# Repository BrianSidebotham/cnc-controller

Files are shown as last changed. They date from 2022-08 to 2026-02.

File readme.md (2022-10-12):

# CNC Controller

This CNC controller is an expansion board for LinuxCNC. See the [electronics](electronics/readme.md) section for the RPi GPIO expansion board suitable for use with LinuxCNC using the [configuration](linuxcnc-configuration/denford-orac-rpi/readme.md).

The PCB is an opto-isolation IO expansion board featuring:

- 16 Opto-isolated outputs (With indicator LED)
- 8 opto-isolated inputs (With indicator LED)
- 2 0-10V analogue outputs connected to two of the opto-isolated outputs

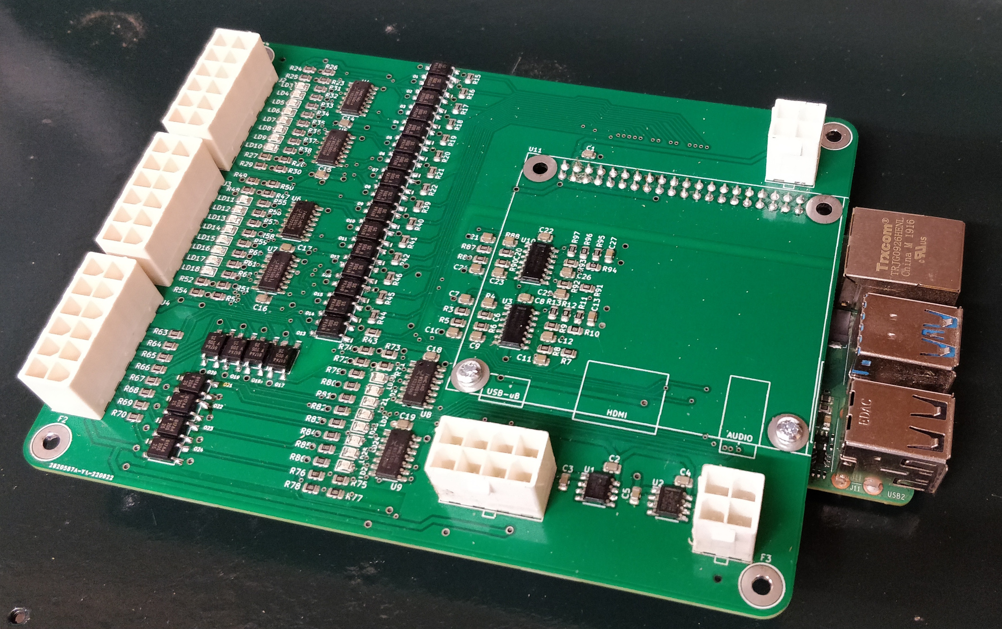
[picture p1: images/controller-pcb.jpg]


## KiCAD Parts Library

This project relies on my KiCAD parts library. So you will need to also clone a copy of my
[KiCAD parts library](https://github.com/BrianSidebotham/kicad-parts).

Then, you can tell KiCAD where to find the parts library by creating a new environment
variable called `KICAD_BJS_KICAD_PARTS` and set the value to the path to the parts library.

If you get the value or variable name wrong you'll see a lot of missing symbols in the
project.

## Build LinuxCNC

You can go ahead and download the LinuxCNC Distribution or else you can build yourself an up-to-date version.

In order to get an up-to-date version, download the LinuxCNC RPi image and write it to an SD Card.

Boot the card and then do the following to update the LinuxCNC package:

```shell
$ wget https://www.linuxcnc.org/dists/buster/2.8-rtpreempt/binary-armhf/linuxcnc-uspace_2.8.4_armhf.deb
$ sudo dpkg -i ./linuxcnc-uspace_2.8.4_armhf.deb
```

## Future Buildroot

In order to build an OS specifically for LinuxCNC you can use the following instructions:

>**WARNING**: These instructions are for future use, do not use yet.

```shell
$ wget https://buildroot.org/downloads/buildroot-2022.02.5.tar.gz
$ tar xf buildroot-2022.02.5.tar.gz
$ cd buildroot-2022.02.5
$ make raspberrypi4_64_defconfig
```

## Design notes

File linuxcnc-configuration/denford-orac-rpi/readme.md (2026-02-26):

# Denford ORAC Linux CNC Configuration

This directory contains HAL files for the hardware in this project and specifically for Denford ORAC hardware.

## Getting Started

Download the Linux CNC 2.9.8 RPI4 or RPI5 image with PREEMPT_RT from the linuxcnc downloads section

> [!NOTE]
> The difference between an RPi4 and RPi5 here is significant. I highly recommend you use an
> RPi5 for a linuxcnc machine using this configuration and image, but I have run LinuxCNC 2.9.3
> like this on an RPi4 for a couple of years so it certainly does work.

Write the image to an SD card by extracting it and then writing to the SD card

> [!WARN]
> _PLEASE_ use `lsblk` to determine what block device the SD Card is. For my machine which only has an NVME drive as the root, this enumerates as `/dev/sda` which is extremely risky if as you're about to overwrite a complete disk. Make sure it's the correct one before running the command:

```sh
unzip image_2026-01-21-raspios-lcnc-2.9.8-trixie-arm64.zip 
sudo su -
cat ./2026-01-21-raspios-lcnc-2.9.8-trixie-arm64.img > /dev/sda \
    && sync \
    && eject /dev/sda
```

With the card written, insert it into the Linux CNC RPi and go through the initial setup. I also recommend setting up the ssh service so you can remotely administer the lathe:

```sh
sudo systemctl enable ssh
sudo systemctl start ssh
```

Log in through SSH and disable the hardware intefaces that are defaulted to on so you do not have conflicting GPIO pins. Make sure the following settings are correct in `/boot/firmware/config.txt`:

```
dtparam=i2c_arm=off
dtparam=spi=off
```

Once logged in, you can clone this repository in the home directory and then start up linux CNC. If you've wired everything the same as the schematics and wiring diagram shows, then you can start the linuxcnc session using:

```sh
cd /home/cnc/cnc-controller/linuxcnc-configuration/denford-orac-rpi/
./linuxcnc.sh
```

## LatheMacros Python Dependencies (Debian Trixie)

If the Cycles tab fails with `ValueError: Namespace Rsvg not available`, install the required **system** packages (no venv required):

```sh
sudo apt update
sudo apt install -y python3-gi gir1.2-rsvg-2.0 python3-cairo
```

Optional (removes the non-fatal GTK warning `Failed to load module "canberra-gtk-module"`):

```sh
sudo apt install -y libcanberra-gtk-module libcanberra-gtk3-module
```

Quick verification:

```sh
python3 -c "import gi, cairo; gi.require_version('Rsvg','2.0'); from gi.repository import Rsvg; print('OK: Rsvg + cairo available')"
```

So if you so happen to have a Denford Orac then this'll _just work_.

## Stepper Motor Scales

The stepper motors on the Denford ORAC are standard 1.8deg / step NEMA34 which have `(360 / 1.8)` 200 steps per revolution.

The [MSD752](../manuals/MSD752_stepper_drive.pdf) drivers I'm using have been configured for 4x microstepping to give 800 steps per rev.

The stepper motors do not directly drive the axis, instead they drive the axis through a belt and pulley setup. The [ORAC operating and maintenance manual](../manuals/orac-programming-operating-and-maintenance.pdf) details the size of the pulleys.

### X Axis

For the X cross slide we have the following arrangement

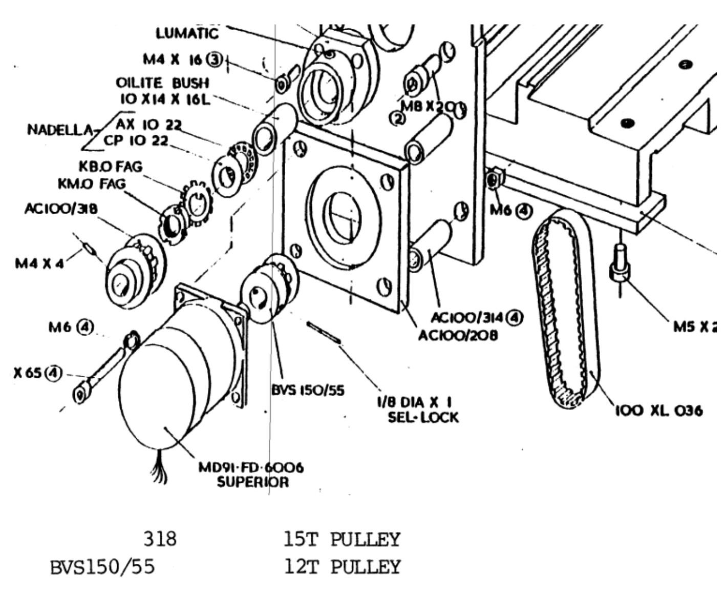
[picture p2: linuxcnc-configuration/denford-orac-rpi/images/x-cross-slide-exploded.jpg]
X Cross-Slide


With the stepper using 800 turns per we can calculate the scale for the x-axis stepper motor stepgen.

The ballscrew is 8mm x 2.5mm pitch

Calculate the number of steps it takes to make a complete revolution of the ballscrew through the pulleys with the motor and driver using 800 steps per rev:

    800 * (15/12) = 1000

One revolution of the ballscrew will move the carriage 2.5mm and we want to know how many steps are required to complete one unit of measurement in the HAL. For me, that's 1mm as everything is metric for me.

    1000 / 2.5 = 400

This gives each step a distance of `0.0025mm`

### Z Axis

For the Z axis we have the following arrangement

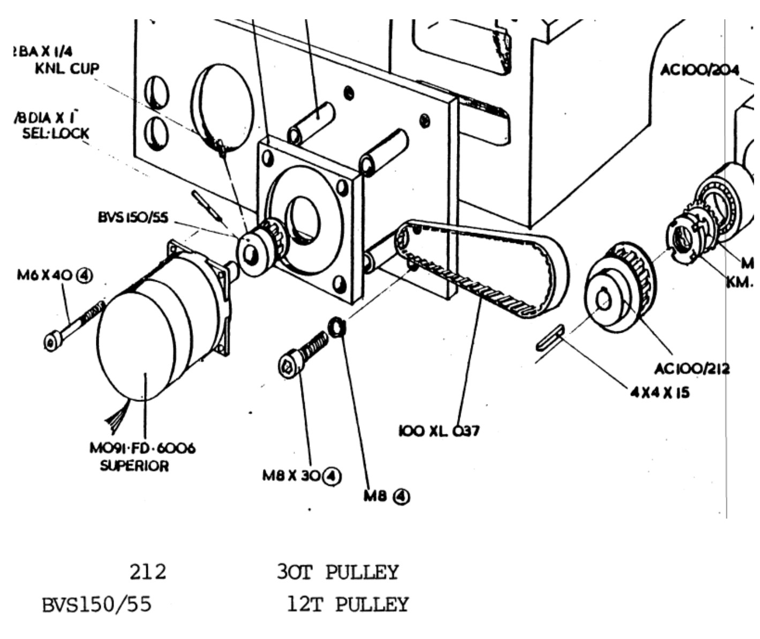
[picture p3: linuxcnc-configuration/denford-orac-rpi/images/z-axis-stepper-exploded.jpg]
Z Axis


The ballscree is 20mm x 5mm pitch

Calculate the number of steps it takes to make a complete revolution of the ballscrew through the pulleys with the motor and driver using 800 steps per rev:

    800 * (30 / 12) = 2000

One revolution of the ballscrew will move the carriage 5mm and we want to know how many steps are required to complete one unit of measurement in the HAL. For me, that's 1mm as everything is metric for me.

    2000 / 5 = 400

This gives each step a distance of `0.0025mm`

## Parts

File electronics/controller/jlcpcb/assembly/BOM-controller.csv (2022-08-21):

Comment | Designator | Footprint | LCSC
1u | C10,C11,C12,C13,C20,C21,C23,C24,C25,C26,C27,C6,C7,C9 | C_0805_2012Metric | C28323
100n | C1,C14,C15,C16,C17,C18,C19,C2,C22,C3,C4,C5,C8 | C_0805_2012Metric | C49678
74HC14 | U4,U5,U6,U7,U8,U9 | SOIC-14_3.9x8.7mm_P1.27mm | C5605
TEVALULOK4W | J1 | te-connectivity_val-u-lok_vertical_4_1586768-4
TEVALULOK4W | J8 | te-connectivity_val-u-lok_vertical_4_1586768-4
TEVALULOK8W | J10 | te-connectivity_val-u-lok_vertical_8_1586768-8
RESISTOR | R1 | R_0805_2012Metric
2k2 | R2 | R_0805_2012Metric
68k | R3 | R_0805_2012Metric
68k | R4 | R_0805_2012Metric
68k | R5 | R_0805_2012Metric
68k | R6 | R_0805_2012Metric
68k | R7 | R_0805_2012Metric
68k | R8 | R_0805_2012Metric
68k | R9 | R_0805_2012Metric
1k5 | R10 | R_0805_2012Metric
120k | R11 | R_0805_2012Metric
120k | R13 | R_0805_2012Metric
1k | R23 | R_0805_2012Metric
MC33204 | U3 | SOIC-14_3.9x8.7mm_P1.27mm
1k5 | R12 | R_0805_2012Metric
VOM617A-4T | O10 | VOMOPTO
VOM617A-4T | O9 | VOMOPTO
78L10SMD | U2 | SOIC-8_3.9x4.9mm_P1.27mm
LED | LD1 | LED_0805_2012Metric
LED | LD2 | LED_0805_2012Metric
LED | LD3 | LED_0805_2012Metric
LED | LD4 | LED_0805_2012Metric
LED | LD10 | LED_0805_2012Metric
LED | LD19 | LED_0805_2012Metric
LED | LD20 | LED_0805_2012Metric
LED | LD21 | LED_0805_2012Metric
LED | LD23 | LED_0805_2012Metric
LED | LD24 | LED_0805_2012Metric
LED | LD25 | LED_0805_2012Metric
LED | LD26 | LED_0805_2012Metric
VOM617A-4T | O13 | VOMOPTO
VOM617A-4T | O14 | VOMOPTO
VOM617A-4T | O16 | VOMOPTO
VOM617A-4T | O17 | VOMOPTO
VOM617A-4T | O19 | VOMOPTO
VOM617A-4T | O20 | VOMOPTO
VOM617A-4T | O21 | VOMOPTO
VOM617A-4T | O23 | VOMOPTO
1k | R26 | R_0805_2012Metric
1k | R28 | R_0805_2012Metric
1k | R30 | R_0805_2012Metric
330R | R34 | R_0805_2012Metric
330R | R35 | R_0805_2012Metric
330R | R36 | R_0805_2012Metric
330R | R37 | R_0805_2012Metric
330R | R38 | R_0805_2012Metric
680R | R39 | R_0805_2012Metric
680R | R40 | R_0805_2012Metric
680R | R41 | R_0805_2012Metric
680R | R42 | R_0805_2012Metric
680R | R43 | R_0805_2012Metric
680R | R44 | R_0805_2012Metric
680R | R45 | R_0805_2012Metric
680R | R46 | R_0805_2012Metric
1k | R47 | R_0805_2012Metric
1k | R48 | R_0805_2012Metric
1k | R49 | R_0805_2012Metric
1k | R50 | R_0805_2012Metric
1k | R51 | R_0805_2012Metric
1k | R52 | R_0805_2012Metric
1k | R53 | R_0805_2012Metric
680R | R63 | R_0805_2012Metric
680R | R64 | R_0805_2012Metric
680R | R65 | R_0805_2012Metric
680R | R68 | R_0805_2012Metric
680R | R69 | R_0805_2012Metric
680R | R70 | R_0805_2012Metric
1k | R71 | R_0805_2012Metric
1k | R73 | R_0805_2012Metric
1k | R74 | R_0805_2012Metric
1k | R75 | R_0805_2012Metric
1k | R76 | R_0805_2012Metric
1k | R77 | R_0805_2012Metric
1k | R78 | R_0805_2012Metric
330R | R79 | R_0805_2012Metric
330R | R80 | R_0805_2012Metric
330R | R81 | R_0805_2012Metric
330R | R82 | R_0805_2012Metric
330R | R83 | R_0805_2012Metric
330R | R84 | R_0805_2012Metric
68k | R88 | R_0805_2012Metric
68k | R89 | R_0805_2012Metric
68k | R90 | R_0805_2012Metric
68k | R91 | R_0805_2012Metric
68k | R92 | R_0805_2012Metric
68k | R93 | R_0805_2012Metric
1k5 | R94 | R_0805_2012Metric
120k | R95 | R_0805_2012Metric
1k5 | R96 | R_0805_2012Metric
120k | R97 | R_0805_2012Metric
330R | R98 | R_0805_2012Metric
MC33204 | U10 | SOIC-14_3.9x8.7mm_P1.27mm
VOM617A-4T | O11 | VOMOPTO
RPI40PIN | U11 | rpi-40pin
330R | R32 | R_0805_2012Metric
330R | R33 | R_0805_2012Metric
330R | R31 | R_0805_2012Metric
VOM617A-4T | O5 | VOMOPTO
VOM617A-4T | O6 | VOMOPTO
VOM617A-4T | O7 | VOMOPTO
VOM617A-4T | O8 | VOMOPTO
680R | R19 | R_0805_2012Metric
680R | R20 | R_0805_2012Metric
680R | R21 | R_0805_2012Metric
680R | R22 | R_0805_2012Metric
1k | R24 | R_0805_2012Metric
1k | R25 | R_0805_2012Metric
1k | R27 | R_0805_2012Metric
1k | R29 | R_0805_2012Metric
LED | LD8 | LED_0805_2012Metric
LED | LD7 | LED_0805_2012Metric
LED | LD6 | LED_0805_2012Metric
TEVALULOK12W | J2 | te-connectivity_val-u-lok_vertical_12_1-1586768-2
LED | LD9 | LED_0805_2012Metric
LED | LD5 | LED_0805_2012Metric
VOM617A-4T | O12 | VOMOPTO
VOM617A-4T | O15 | VOMOPTO
VOM617A-4T | O18 | VOMOPTO
VOM617A-4T | O22 | VOMOPTO
VOM617A-4T | O24 | VOMOPTO
VOM617A-4T | O1 | VOMOPTO
VOM617A-4T | O2 | VOMOPTO
VOM617A-4T | O3 | VOMOPTO
VOM617A-4T | O4 | VOMOPTO
680R | R15 | R_0805_2012Metric
680R | R16 | R_0805_2012Metric
680R | R17 | R_0805_2012Metric
680R | R18 | R_0805_2012Metric
TEVALULOK12W | J3 | te-connectivity_val-u-lok_vertical_12_1-1586768-2
LED | LD12 | LED_0805_2012Metric
LED | LD13 | LED_0805_2012Metric
LED | LD14 | LED_0805_2012Metric
LED | LD15 | LED_0805_2012Metric
LED | LD16 | LED_0805_2012Metric
LED | LD17 | LED_0805_2012Metric
LED | LD18 | LED_0805_2012Metric
330R | R55 | R_0805_2012Metric
330R | R57 | R_0805_2012Metric
330R | R58 | R_0805_2012Metric
330R | R59 | R_0805_2012Metric
330R | R60 | R_0805_2012Metric
330R | R61 | R_0805_2012Metric
330R | R62 | R_0805_2012Metric
LED | LD11 | LED_0805_2012Metric
TEVALULOK12W | J4 | te-connectivity_val-u-lok_vertical_12_1-1586768-2
330R | R56 | R_0805_2012Metric
1k | R54 | R_0805_2012Metric
680R | R66 | R_0805_2012Metric
680R | R67 | R_0805_2012Metric
LED | LD22 | LED_0805_2012Metric
330R | R85 | R_0805_2012Metric
330R | R86 | R_0805_2012Metric
68k | R87 | R_0805_2012Metric
1k | R72 | R_0805_2012Metric
78L05SMD | U1 | SOIC-8_3.9x4.9mm_P1.27mm
330R | R14 | R_0805_2012Metric
M3 | F3 | M3
M3 | F4 | M3
M3 | F2 | M3
M3 | F1 | M3

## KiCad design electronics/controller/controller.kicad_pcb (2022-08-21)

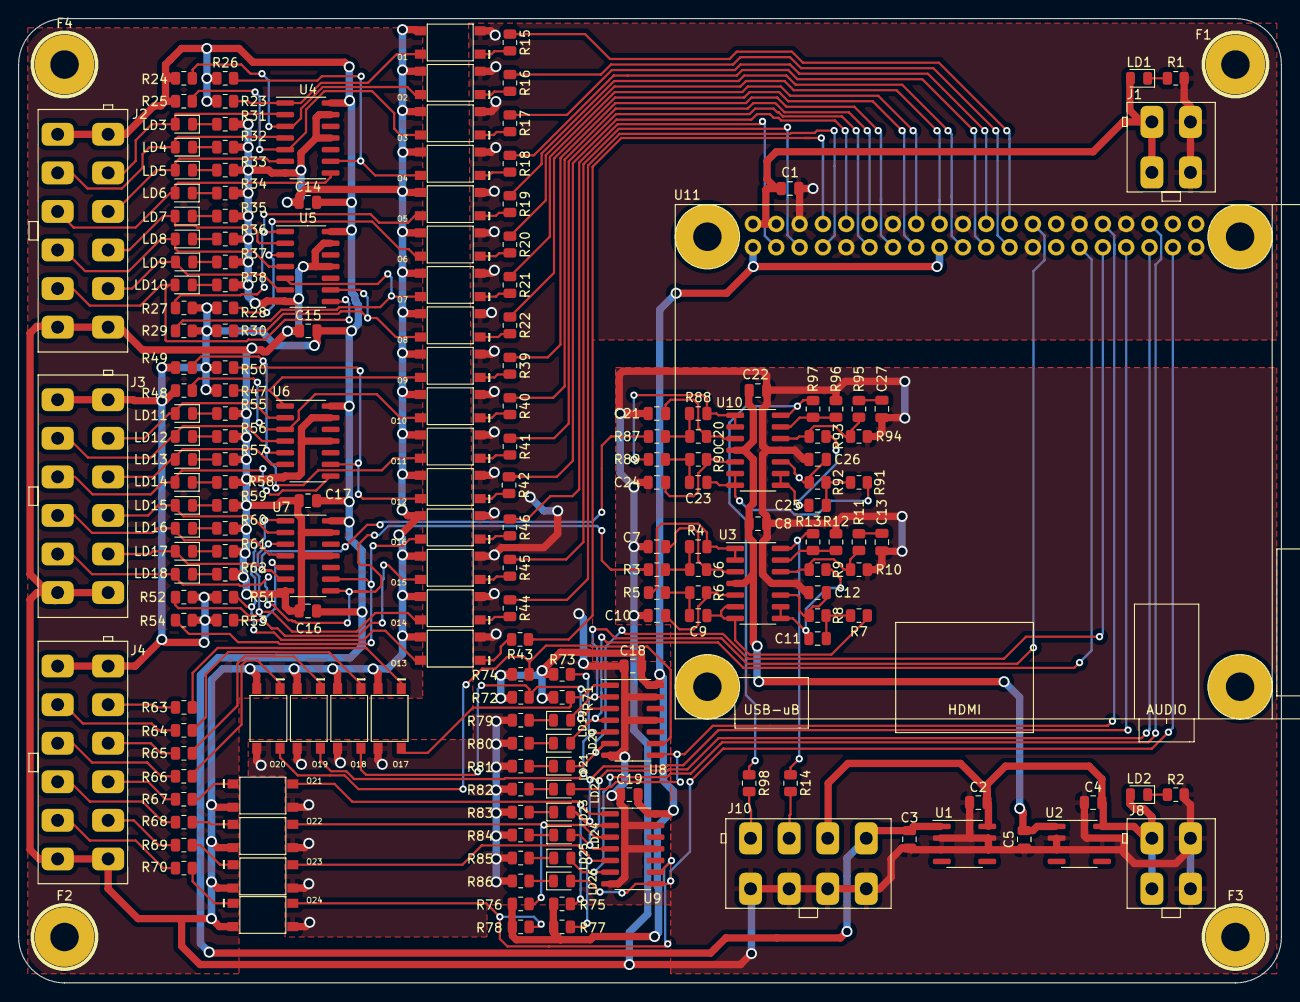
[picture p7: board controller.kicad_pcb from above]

Board: 2 copper layers, 137.5 x 105.0 mm, 196 parts (0 on the bottom side), 157 nets.

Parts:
C1, C2, C3, C4, C5, C8, C14, C15, C16, C17, C18, C19, C22: 100n; C_0805_2012Metric
C6, C7, C9, C10, C11, C12, C13, C20, C21, C23, C24, C25, C26, C27: 1u; C_0805_2012Metric
F1, F2, F3, F4: M3
J1, J8: TEVALULOK4W; te-connectivity_val-u-lok_vertical_4_1586768-4
J2, J3, J4: TEVALULOK12W; te-connectivity_val-u-lok_vertical_12_1-1586768-2
J10: TEVALULOK8W; te-connectivity_val-u-lok_vertical_8_1586768-8
LD1, LD2, LD3, LD4, LD5, LD6, LD7, LD8, LD9, LD10, LD11, LD12, LD13, LD14, LD15, LD16, LD17, LD18, LD19, LD20, LD21, LD22, LD23, LD24, LD25, LD26: LED; LED_0805_2012Metric
O1, O2, O3, O4, O5, O6, O7, O8, O9, O10, O11, O12, O13, O14, O15, O16, O17, O18, O19, O20, O21, O22, O23, O24: VOM617A-4T; VOMOPTO
R1: RESISTOR; R_0805_2012Metric
R2: 2k2; R_0805_2012Metric
R3, R4, R5, R6, R7, R8, R9, R87, R88, R89, R90, R91, R92, R93: 68k; R_0805_2012Metric
R10, R12, R94, R96: 1k5; R_0805_2012Metric
R11, R13, R95, R97: 120k; R_0805_2012Metric
R14, R31, R32, R33, R34, R35, R36, R37, R38, R55, R56, R57, R58, R59, R60, R61, R62, R79, R80, R81, R82, R83, R84, R85, R86, R98: 330R; R_0805_2012Metric
R15, R16, R17, R18, R19, R20, R21, R22, R39, R40, R41, R42, R43, R44, R45, R46, R63, R64, R65, R66, R67, R68, R69, R70: 680R; R_0805_2012Metric
R23, R24, R25, R26, R27, R28, R29, R30, R47, R48, R49, R50, R51, R52, R53, R54, R71, R72, R73, R74, R75, R76, R77, R78: 1k; R_0805_2012Metric
U1: 78L05SMD; SOIC-8_3.9x4.9mm_P1.27mm
U2: 78L10SMD; SOIC-8_3.9x4.9mm_P1.27mm
U3, U10: MC33204; SOIC-14_3.9x8.7mm_P1.27mm
U4, U5, U6, U7, U8, U9: 74HC14; SOIC-14_3.9x8.7mm_P1.27mm
U11: RPI40PIN; rpi-40pin

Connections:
+10V: C5.2, C8.2, C22.2, U2.1 (VO), U3.4 (VCC), U10.4 (VCC)
+12V: C2.2, C4.2, J8.1, J8.2, J10.5, LD2.2, U1.8 (VIN), U2.8 (VIN)
/0-10V-CH1: J10.1, R98.2
/0-10V-CH2: J10.3, R14.2
/IN1: J4.3, R63.1
/IN2: J4.4, R64.1
/IN3: J4.5, R65.1
/IN4: J4.6, R66.1
/IN5: J4.7, R67.1
/IN6: J4.8, R68.1
/IN7: J4.9, R69.1
/IN8: J4.10, R70.1
/OUT1: J2.3, LD3.2, U4.2
/OUT2: J2.4, LD4.2, U4.4
/OUT3: J2.5, LD5.2, U4.6
/OUT4: J2.6, LD6.2, U4.8
/OUT5: J2.7, LD7.2, U5.2
/OUT6: J2.8, LD8.2, U5.4
/OUT7: J2.9, LD9.2, U5.6
/OUT8: J2.10, LD10.2, U5.8
/OUT9: J3.3, LD11.2, U6.2
/OUT10: J3.4, LD12.2, U6.4
/OUT11: J3.5, LD13.2, U6.6
/OUT12: J3.6, LD14.2, U6.8
/OUT13: J3.7, LD15.2, U7.2
/OUT14: J3.8, LD16.2, U7.4
/OUT15: J3.9, LD17.2, R87.1, U7.6
/OUT16: J3.10, LD18.2, R3.1, U7.8
/RPIIN1: LD19.2, U8.2, U11.26 (GPIO7)
/RPIIN2: LD20.2, U8.4, U11.29 (GPIO5)
/RPIIN3: LD21.2, U8.6, U11.31 (GPIO6)
/RPIIN4: LD22.2, U8.8, U11.32 (GPIO12)
/RPIIN5: LD23.2, U9.2, U11.33 (GPIO13)
/RPIIN6: LD24.2, U9.4, U11.35 (GPIO19)
/RPIIN7: LD25.2, U9.6, U11.36 (GPIO16)
/RPIIN8: LD26.2, U9.8, U11.37 (GPIO26)
/RPIOUT1: R15.1, U11.24 (GPIO8)
/RPIOUT2: R16.1, U11.23 (GPIO11)
/RPIOUT3: R17.1, U11.22 (GPIO25)
/RPIOUT4: R18.1, U11.21 (GPIO9)
/RPIOUT5: R19.1, U11.19 (GPIO10)
/RPIOUT6: R20.1, U11.18 (GPIO24)
/RPIOUT7: R21.1, U11.16 (GPIO23)
/RPIOUT8: R22.1, U11.15 (GPIO22)
/RPIOUT9: R39.1, U11.13 (GPIO27)
/RPIOUT10: R40.1, U11.12 (GPIO18)
/RPIOUT11: R41.1, U11.11 (GPIO17)
/RPIOUT12: R42.1, U11.10 (GPIO15)
/RPIOUT13: R43.1, U11.8 (GPIO14)
/RPIOUT14: R44.1, U11.7 (GPIO4)
/RPIOUT15: R45.1, U11.5 (GPIO3)
/RPIOUT16: R46.1, U11.3 (GPIO2)
/rpiconnectivity/3V3: C18.2, C19.2, R71.2, R72.2, R73.2, R74.2, R75.2, R76.2, R77.2, R78.2, U8.14 (VCC), U9.14 (VCC), U11.1 (3V3), U11.17 (3V3)
GND: C1.1, C18.1, C19.1, J1.3, J1.4, O1.2, O2.2, O3.2, O4.2, O5.2, O6.2, O7.2, O8.2, O9.2, O10.2, O11.2, O12.2, O13.2, O14.2, O15.2, O16.2, O17.3, O18.3, O19.3, O20.3, O21.3, O22.3, O23.3, O24.3, R1.2, R79.2, R80.2, R81.2, R82.2, R83.2, R84.2, R85.2, R86.2, U8.7 (GND), U8.11, U8.13, U9.7 (GND), U9.11, U9.13, U11.6 (GND), U11.9 (GND), U11.14 (GND), U11.20 (GND), U11.25 (GND), U11.30 (GND), U11.34 (GND), U11.39 (GND)
unnamed: C6.1, R5.1, U3.1, U3.2 (-)
unnamed: C6.2, R3.2, R4.1
unnamed: C7.2, R4.2, U3.3 (+)
unnamed: C9.1, R7.1, U3.6 (-), U3.7
unnamed: C9.2, R5.2, R6.1
unnamed: C10.2, R6.2, U3.5 (+)
unnamed: C11.1, R9.1, U3.8, U3.9 (-)
unnamed: C11.2, R7.2, R8.1
unnamed: C12.2, R8.2, U3.10 (+)
unnamed: C13.2, R11.2
unnamed: C20.1, R89.1, U10.1, U10.2 (-)
unnamed: C20.2, R87.2, R88.1
unnamed: C21.2, R88.2, U10.3 (+)
unnamed: C23.1, R91.1, U10.6 (-), U10.7
unnamed: C23.2, R89.2, R90.1
unnamed: C24.2, R90.2, U10.5 (+)
unnamed: C25.1, R93.1, U10.8, U10.9 (-)
unnamed: C25.2, R91.2, R92.1
unnamed: C26.2, R92.2, U10.10 (+)
unnamed: C27.2, R95.2
unnamed: LD1.1, R1.1
unnamed: LD2.1, R2.1
unnamed: LD3.1, R31.1
unnamed: LD4.1, R32.1
unnamed: LD5.1, R33.1
unnamed: LD6.1, R34.1
unnamed: LD7.1, R35.1
unnamed: LD8.1, R36.1
unnamed: LD9.1, R37.1
unnamed: LD10.1, R38.1
unnamed: LD11.1, R55.1
unnamed: LD12.1, R56.1
unnamed: LD13.1, R57.1
unnamed: LD14.1, R58.1
unnamed: LD15.1, R59.1
unnamed: LD16.1, R60.1
unnamed: LD17.1, R61.1
unnamed: LD18.1, R62.1
unnamed: LD19.1, R79.1
unnamed: LD20.1, R80.1
unnamed: LD21.1, R81.1
unnamed: LD22.1, R82.1
unnamed: LD23.1, R83.1
unnamed: LD24.1, R84.1
unnamed: LD25.1, R85.1
unnamed: LD26.1, R86.1
unnamed: O1.1, R15.2
unnamed: O1.4, R23.1, U4.1
unnamed: O2.1, R16.2
unnamed: O2.4, R24.1, U4.3
unnamed: O3.1, R17.2
unnamed: O3.4, R25.1, U4.5
unnamed: O4.1, R18.2
unnamed: O4.4, R26.1, U4.9
unnamed: O5.1, R19.2
unnamed: O5.4, R27.1, U5.1
unnamed: O6.1, R20.2
unnamed: O6.4, R28.1, U5.3
unnamed: O7.1, R21.2
unnamed: O7.4, R29.1, U5.5
unnamed: O8.1, R22.2
unnamed: O8.4, R30.1, U5.9
unnamed: O9.1, R39.2
unnamed: O9.4, R47.1, U6.1
unnamed: O10.1, R40.2
unnamed: O10.4, R48.1, U6.3
unnamed: O11.1, R41.2
unnamed: O11.4, R49.1, U6.5
unnamed: O12.1, R42.2
unnamed: O12.4, R50.1, U6.9
unnamed: O13.1, R43.2
unnamed: O13.4, R51.1, U7.1
unnamed: O14.1, R44.2
unnamed: O14.4, R52.1, U7.3
unnamed: O15.1, R45.2
unnamed: O15.4, R53.1, U7.5
unnamed: O16.1, R46.2
unnamed: O16.4, R54.1, U7.9
unnamed: O17.1, R63.2
unnamed: O17.4, R71.1, U8.1
unnamed: O18.1, R64.2
unnamed: O18.4, R72.1, U8.3
unnamed: O19.1, R65.2
unnamed: O19.4, R73.1, U8.5
unnamed: O20.1, R66.2
unnamed: O20.4, R74.1, U8.9
unnamed: O21.1, R67.2
unnamed: O21.4, R75.1, U9.1
unnamed: O22.1, R68.2
unnamed: O22.4, R76.1, U9.3
unnamed: O23.1, R69.2
unnamed: O23.4, R77.1, U9.5
unnamed: O24.1, R70.2
unnamed: O24.4, R78.1, U9.9
unnamed: R9.2, R10.1, R11.1, U3.12 (+)
unnamed: R12.1, R13.1, U3.13 (-)
unnamed: R13.2, R14.1, U3.14
unnamed: R93.2, R94.1, R95.1, U10.12 (+)
unnamed: R96.1, R97.1, U10.13 (-)
unnamed: R97.2, R98.1, U10.14
VCC: C1.2, J1.1, J1.2, LD1.2, U11.2 (5V), U11.4 (5V)
VDD: C3.2, C14.2, C15.2, C16.2, C17.2, J2.1, J2.2, J3.1, J3.2, J4.1, J4.2, J10.7, R23.2, R24.2, R25.2, R26.2, R27.2, R28.2, R29.2, R30.2, R47.2, R48.2, R49.2, R50.2, R51.2, R52.2, R53.2, R54.2, U1.1 (VO), U4.14 (VCC), U5.14 (VCC), U6.14 (VCC), U7.14 (VCC)
VSS: C2.1, C3.1, C4.1, C5.1, C7.1, C8.1, C10.1, C12.1, C13.1, C14.1, C15.1, C16.1, C17.1, C21.1, C22.1, C24.1, C26.1, C27.1, J2.11, J2.12, J3.11, J3.12, J4.11, J4.12, J8.3, J8.4, J10.2, J10.4, J10.6, J10.8, O1.3, O2.3, O3.3, O4.3, O5.3, O6.3, O7.3, O8.3, O9.3, O10.3, O11.3, O12.3, O13.3, O14.3, O15.3, O16.3, O17.2, O18.2, O19.2, O20.2, O21.2, O22.2, O23.2, O24.2, R2.2, R10.2, R12.2, R31.2, R32.2, R33.2, R34.2, R35.2, R36.2, R37.2, R38.2, R55.2, R56.2, R57.2, R58.2, R59.2, R60.2, R61.2, R62.2, R94.2, R96.2, U1.2 (GND), U1.3 (GND), U1.6 (GND), U1.7 (GND), U2.2 (GND), U2.3 (GND), U2.6 (GND), U2.7 (GND), U3.11 (VEE), U4.7 (GND), U4.11, U4.13, U5.7 (GND), U5.11, U5.13, U6.7 (GND), U6.11, U6.13, U7.7 (GND), U7.11, U7.13, U10.11 (VEE)

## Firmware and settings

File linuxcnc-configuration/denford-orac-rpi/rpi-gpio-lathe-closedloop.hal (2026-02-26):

# CNC Controller HAL file to match PCB hardware (16 outputs, 8 inputs)
# This HAL file is for a Lathe machine and features:
# - 2 axis stepper control (X and Z axis)
# - Limit switch support
# - Spindle 0-10V PWM output
# - Spindle synch and speed feedback for closed loop control
#
# The RPI GPIO driver is used for IO

loadrt [KINS]KINEMATICS

loadrt [EMCMOT]EMCMOT base_period_nsec=[EMCMOT]BASE_PERIOD servo_period_nsec=[EMCMOT]SERVO_PERIOD num_joints=[KINS]JOINTS
loadrt not count=4

# scale and lowpass are used in the postUI hal configuration for calculating the spindle speed input
loadrt scale count=1
loadrt lowpass count=1
loadrt abs count=1
loadrt sum2 count=2
loadrt pid names=spindle-pid

loadrt charge_pump
net estop-out charge-pump.enable iocontrol.0.user-enable-out
net charge-pump <= charge-pump.out

# Configure all inputs and outputs to match the hardware that we have. The interface PCB has 16 outputs and
# 8 inputs. The gpio driver is configured with two values that set the direction of a GPIO line and a mask
# of GPIO lines that are being used.
# gpio pins ( not rpi pins! )
# 2 2  2 2 2 2  2 2 1 1  1 1 1 1  1 1 1 1
# 7 6  5 4 3 2  1 0 9 8  7 6 5 4  3 2 1 0  9 8 7 6  5 4 3 2  (gpio1 & 0 are not used)

# 1 0  1 1 1 1  0 0 0 1  1 0 1 1  0 0 1 1  1 1 0 0  0 1 1 1  dir     mask (0 means in   1 means out)
# 0 0  0 0 0 0  1 1 0 0  0 0 0 0  0 0 0 0  0 0 0 0  0 0 0 0  exclude mask (0 means use  1 means dont use)

loadrt hal_gpio inputs=GPIO5,GPIO6,GPIO7,GPIO12,GPIO13,GPIO16,GPIO19,GPIO26 outputs=GPIO2,GPIO3,GPIO4,GPIO8,GPIO9,GPIO10,GPIO11,GPIO14,GPIO15,GPIO17,GPIO18,GPIO22,GPIO23,GPIO24,GPIO25,GPIO27 invert=GPIO4

# beware gpio 21 and 22 are still reversed, they control rpins 15&50 and are backwards almost everywhere in rpi docs
# easy to see and check with 'show pins hal_pi_gpio*

# The hardware from the PCB is configured as follows:

# GPIO | info   | Pn | PCB SIG | CUSTOM_FUNCTION
#
#   0  | ID_SDA | 27 | Unused  |
#   1  | ID_SCL | 28 | Unused  |
#   2  | GPIO2  | 3  | OUT16   | PWM CH 2 - Spindle 0-10V
#   3  | GPIO3  | 5  | OUT15   | PWM CH 1
#   4  | GPIO4  | 7  | OUT14   | Spindle Enable ( On when HIGH ) - also used as the spindle on signal for the encoder feedback loop
#   5  | GPIO5  | 29 | IN2     | SPINDLE POSITION
#   6  | GPIO6  | 31 | IN3     | LIMIT
#   7  | GPIO7  | 26 | IN1     | SPINDLE INDEX

#   8  | GPIO8  | 24 | OUT1    | X Enable
#   9  | GPIO9  | 21 | OUT4    |
#  10  | GPIO10 | 19 | OUT5    | Z Enable
#  11  | GPIO11 | 23 | OUT2    | X DIR
#  12  | GPIO12 | 32 | IN4     | X Limit
#  13  | GPIO13 | 33 | IN5     | Z Limit
#  14  | GPIO14 | 8  | OUT13   |
#  15  | GPIO15 | 10 | OUT12   |

#  16  | GPIO16 | 36 | IN7     |
#  17  | GPIO17 | 11 | OUT11   |
#  18  | GPIO18 | 12 | OUT10   |
#  19  | GPIO19 | 35 | IN6     |
#  20  | GPIO20 | 38 | Unused  |
#  21  | GPIO21 | 40 | Unused  |
#  22  | GPIO22 | 5  | OUT8    |
#  23  | GPIO23 | 16 | OUT7    | Z STEP

#  24  | GPIO24 | 18 | OUT6    | Z DIR
#  25  | GPIO25 | 22 | OUT3    | X STEP
#  26  | GPIO26 | 37 | IN8     |
#  27  | GPIO27 | 13 | OUT9    |

loadrt stepgen step_type=0,0,0

# DEBOUNCE Probe und Limits
loadrt debounce cfg=4
setp debounce.0.delay 10
addf debounce.0 base-thread

addf hal_gpio.read  base-thread
addf hal_gpio.write base-thread
addf stepgen.make-pulses base-thread
addf charge-pump base-thread
addf not.0 servo-thread
addf not.1 servo-thread
addf not.2 servo-thread
addf abs.0 servo-thread
addf scale.0 servo-thread
addf sum2.0 servo-thread
addf sum2.1 servo-thread
addf spindle-pid.do-pid-calcs servo-thread
addf lowpass.0 servo-thread
addf stepgen.capture-position servo-thread
addf motion-command-handler servo-thread
addf motion-controller servo-thread
addf stepgen.update-freq servo-thread

# In order to have spindle feedback we need to use the encoder functions
# See the Spindle Feedback section of the docs: https://linuxcnc.org/docs/html/examples/spindle.html

loadrt encoder num_chan=1
addf encoder.update-counters   base-thread
addf encoder.capture-position  servo-thread

loadrt pwmgen output_type=0
addf pwmgen.update             servo-thread
addf pwmgen.make-pulses        base-thread

# Set the spindle's top speed in RPM
# 0% PWM = 120 RPM and 100% PWM = 1600 RPM, so the PWM span is 1480 RPM
setp pwmgen.0.scale            1480

# Apply spindle command offset before PWM conversion:
#   120 RPM -> 0% PWM
#   1600 RPM -> 100% PWM
setp sum2.0.gain0 1
setp sum2.0.gain1 -1
setp sum2.0.in1   120

# Closed-loop spindle correction path:
#   spindle_cmd_closed = spindle_cmd + pid_correction
setp sum2.1.gain0 1
setp sum2.1.gain1 1

# PID tuning (starting values, tune on machine if needed)
setp spindle-pid.Pgain 0.10
setp spindle-pid.Igain 0.12
setp spindle-pid.Dgain 0
setp spindle-pid.bias 0
setp spindle-pid.maxoutput 300

# load a near component and attach it to a thread
loadrt near
addf near.0 servo-thread

# Set the PWM base frequency in Hz. The filter in the hardware is optimised for 10Hz
setp pwmgen.0.pwm-freq         10
#setp pwmgen.0.offset           0.025

net spindle-speed-cmd spindle.0.speed-out => spindle-pid.command sum2.1.in0 near.0.in2
net spindle-on => spindle-pid.enable
net spindle-speed-corr spindle-pid.output => sum2.1.in1
net spindle-speed-cmd-closed sum2.1.out => sum2.0.in0
net spindle-speed-cmd-offset sum2.0.out => pwmgen.0.value
net spindle-on spindle.0.on => pwmgen.0.enable hal_gpio.GPIO4-out
#net spindle.0.on => not.2.in
#net not.2.out => hal_gpio.GPIO4-out

net spindle-pwm pwmgen.0.pwm => hal_gpio.GPIO2-out

# The standard Denford Orac position disc has 48 pulses per revolution
setp encoder.0.position-scale 48

# This is not a quadrature encoder (with A and B signals) so we use just a simple counter mode
setp encoder.0.counter-mode true

# Connect the HAL encoder outputs to LinuxCNC
net spindle-position encoder.0.position => spindle.0.revs
net spindle-velocity encoder.0.velocity => spindle.0.speed-in
net spindle-index-enable encoder.0.index-enable => spindle.0.index-enable

# Hook the spindle encoder HAL to the physical pins
net spindle-phase-a encoder.0.phase-A <= hal_gpio.GPIO5-in
net spindle-phase-b encoder.0.phase-B
net spindle-index encoder.0.phase-Z <= hal_gpio.GPIO7-in

# Convert revolutions per second (RPS) to revolutions per minute (RPM)
setp scale.0.gain 60
net spindle-velocity => scale.0.in
net spindle-velocity-rpm <= scale.0.out => spindle-pid.feedback

# connect one input to the encoder-measured spindle speed
net spindle-velocity-rpm => near.0.in1

# connect the output to the spindle-at-speed input
net spindle-at-speed spindle.0.at-speed <= near.0.out

# set the spindle speed inputs to agree if within 1%
setp near.0.scale 1.15

# Stepper signal setup
net xenable => not.0.in
net notxenable not.0.out => hal_gpio.GPIO8-out
net xdir  stepgen.0.dir  => hal_gpio.GPIO11-out
net xstep stepgen.0.step => hal_gpio.GPIO25-out

net zenable => not.1.in
net notzenable not.1.out => hal_gpio.GPIO10-out
net zstep stepgen.1.step => hal_gpio.GPIO23-out
net zdir  stepgen.1.dir  => hal_gpio.GPIO24-out

# i use GPIO 17 27 22 for xlim ylim zlim , thats rpins  11,13,15 resp
# ( one signal used 3 ways, used for + and - lims, used for home also )
# now add limits and homing for x
net xlimit-switch hal_gpio.GPIO12-in => debounce.0.0.in
net xlim debounce.0.0.out => joint.0.neg-lim-sw-in joint.0.pos-lim-sw-in joint.0.home-sw-in

# now add limits and homing for z
net zlimit-switch hal_gpio.GPIO13-in => debounce.0.1.in
net zlim debounce.0.1.out => joint.1.neg-lim-sw-in joint.1.pos-lim-sw-in joint.1.home-sw-in

setp stepgen.0.position-scale [JOINT_0]SCALE
setp stepgen.0.steplen 1000
setp stepgen.0.stepspace 1000
setp stepgen.0.dirhold 10000
setp stepgen.0.dirsetup 1000
setp stepgen.0.maxaccel [JOINT_0]STEPGEN_MAXACCEL
net xpos-cmd joint.0.motor-pos-cmd => stepgen.0.position-cmd
net xpos-fb stepgen.0.position-fb => joint.0.motor-pos-fb
net xstep <= stepgen.0.step
net xdir <= stepgen.0.dir
net xenable joint.0.amp-enable-out => stepgen.0.enable

setp stepgen.1.position-scale [JOINT_1]SCALE
setp stepgen.1.steplen 1000
setp stepgen.1.stepspace 1000
setp stepgen.1.dirhold 10000
setp stepgen.1.dirsetup 1000
setp stepgen.1.maxaccel [JOINT_1]STEPGEN_MAXACCEL
net zpos-cmd joint.1.motor-pos-cmd => stepgen.1.position-cmd
net zpos-fb stepgen.1.position-fb => joint.1.motor-pos-fb
net zstep <= stepgen.1.step
net zdir <= stepgen.1.dir
net zenable joint.1.amp-enable-out => stepgen.1.enable

net estop-out <= iocontrol.0.user-enable-out
net estop-out => iocontrol.0.emc-enable-in

loadusr -W hal_manualtoolchange
net tool-change iocontrol.0.tool-change => hal_manualtoolchange.change
net tool-changed iocontrol.0.tool-changed <= hal_manualtoolchange.changed
net tool-number iocontrol.0.tool-prep-number => hal_manualtoolchange.number
net tool-prepare-loopback iocontrol.0.tool-prepare => iocontrol.0.tool-prepared

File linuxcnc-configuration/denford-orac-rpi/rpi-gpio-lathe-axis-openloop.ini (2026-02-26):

# Generated by stepconf at Wed Sep 26 07:50:40 2012
# If you make changes to this file, they will be
# overwritten when you run stepconf again
# 20 jun 2018 adding needle motor control thru motion.spindle-on
# will later add TDC snesor so needle is in safe position for moving without cutting

[EMC]
# The version string for this INI file.
VERSION = 1.1
MACHINE = Denford Orac
DEBUG = 0

[DISPLAY]
DISPLAY = axis
PREFERENCE_FILE_PATH = gmoccapy_preferences
EDITOR = scite
POSITION_OFFSET = RELATIVE
POSITION_FEEDBACK = ACTUAL
MAX_FEED_OVERRIDE = 1.2
INTRO_GRAPHIC = linuxcnc.gif
INTRO_TIME = 5
PROGRAM_PREFIX = nc_files/
#INCREMENTS = .1in .05in .01in .005in .001in .0005in .0001in
INCREMENTS = 10mm 5mm 2mm 1mm 0.5mm 0.1mm 0.05mm 0.01mm
EMBED_TAB_NAME = Cycles
EMBED_TAB_LOCATION = ntb_preview
EMBED_TAB_COMMAND = halcmd loadusr -Wn gladevcp gladevcp -c gladevcp -U notouch=0 -U norun=0 -u macros/LatheMacros/lathehandler.py -x {XID} macros/LatheMacros/lathemacro.ui
DEFAULT_LINEAR_VELOCITY = 25
MIN_LINEAR_VELOCITY = 0
MAX_LINEAR_VELOCITY = 125
DEFAULT_SPINDLE_0_SPEED = 1000
MIN_SPINDLE_0_SPEED = 200
MAX_SPINDLE_0_SPEED = 1800
MAX_SPINDLE_0_OVERRIDE = 1
MIN_SPINDLE_0_OVERRIDE = 0.5

CYCLE_TIME = 200
LATHE = 1
BACK_TOOL_LATHE = 1

[FILTER]
PROGRAM_EXTENSION = .png,.gif,.jpg Greyscale Depth Image
PROGRAM_EXTENSION = .py Python Script
png = image-to-gcode
gif = image-to-gcode
jpg = image-to-gcode
py = python

[RS274NGC]
PARAMETER_FILE = linuxcnc.var
RS274NGC_STARTUP_CODE = G18
SUBROUTINE_PATH = /usr/share/doc/linuxcnc/examples/sample-configs/sim/gmoccapy/macros:macros:macros/LatheMacros

[EMCMOT]
EMCMOT = motmod
COMM_TIMEOUT = 1.0
BASE_PERIOD = 50000
SERVO_PERIOD = 1000000

[TASK]
TASK = milltask
CYCLE_TIME = 0.010

[HAL]
HALFILE = rpi-gpio-lathe-openloop.hal
POSTGUI_HALFILE = rpi-gpio-lathe-postui-gmoccapy.hal
HALUI = halui

[HALUI]
#No Content

[TRAJ]
AXES = 2
ANGULAR_UNITS = degree
COORDINATES = X Z
# This is used when jogging an axis
DEFAULT_LINEAR_ACCELERATION = 20.0
LINEAR_UNITS =  mm
POSITION_FILE=/home/cnc/linuxcnc-position.txt

# In order to determine the maximum velocities we can use the base period
# of 50000ns and determine that if the RPi needs two periods per step we
# can end up with the following numbe of steps per second
#
#     1 / 50000 x 10^-9 = 20000 / 2 = 10000 steps per second
#
# For each axis on the Denford ORAC we have a step distance of 0.0025mm.
# Therefore max velocity is 10000 * 0.0025 = 25mm which is 1500mm per minute.
# The Denford ORAC is spec'd at 1200mm/min maximum ()
MAX_LINEAR_VELOCITY = 20
NO_FORCE_HOMING = 1
SPINDLES = 1

[EMCIO]
EMCIO = io
CYCLE_TIME = 0.100
TOOL_TABLE = tool.tbl

[KINS]
KINEMATICS = trivkins coordinates=xz
JOINTS = 2

[AXIS_X]
MIN_LIMIT = -50.0
MAX_LIMIT = 50.0
MAX_VELOCITY = 20.0
MAX_ACCELERATION = 20.0

[JOINT_0]
TYPE = LINEAR
MAX_VELOCITY = 20.0
MAX_ACCELERATION = 20.0
STEPGEN_MAXACCEL = 25.0
SCALE = 400
FERROR = 5.25
MIN_FERROR = 0.25
MIN_LIMIT = -50.0
MAX_LIMIT = 50.0

HOME = 0.0
HOME_OFFSET = 5.0

# temp  no homing for rpi while no real hdwr
HOME_SEARCH_VEL = 10.00
HOME_LATCH_VEL = 0.25
HOME_USE_INDEX = NO
HOME_IGNORE_LIMITS = YES
HOME_FINAL_VEL = 10.0

# temp  no homing for rpi while no real hdwr
# HOME_SEQUENCE = 1

[AXIS_Z]
MIN_LIMIT = -250
MAX_LIMIT = 250
MAX_VELOCITY = 20
MAX_ACCELERATION = 20.0

[JOINT_1]
TYPE = LINEAR
MAX_VELOCITY = 20
MAX_ACCELERATION = 20.0
STEPGEN_MAXACCEL = 25.0
SCALE = 400
FERROR = 5.25
MIN_FERROR = 0.25
MIN_LIMIT = -250.0
MAX_LIMIT = 250.0

HOME = 0.0
HOME_OFFSET = 5.0

# temp  no homing for rpi while no real hdwr
HOME_SEARCH_VEL = 10.00
HOME_LATCH_VEL = .25
HOME_USE_INDEX = NO
HOME_IGNORE_LIMITS = YES
HOME_FINAL_VEL = 5.0

# temp  no homing for rpi while no real hdwr
# HOME_SEQUENCE = 1

[MACROS]
MACRO = i_am_lost
MACRO = halo_world
MACRO = jog_around
MACRO = increment xinc yinc
MACRO = go_to_position X-pos Y-pos Z-pos

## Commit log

2022-08-20 Update PCB design to nearly finished design.
    [axis-control.sch, controller.kicad_pcb, controller.kicad_sch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]
2022-08-20 PCB zones added and fully routed
    [controller.kicad_pcb, controller.kicad_sch]
2022-08-21 Add JLCPCB fabrication output post order
    [BOM-controller.csv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]
2022-08-21 Add Denford Orac Linux CNC configuration
    [rpi-gpio-lathe-postui.hal, rpi-gpio-lathe.hal, rpi-gpio-lathe.ini]
2022-09-07 Add user manual for the VFD motor drive
2022-09-08 Update pin direction configuration and mask to match hardware
    [rpi-gpio-lathe.hal]
2022-09-08 Remove and ignore kicad prl files which contain user settings not required for vcs
2022-09-08 Update HAL to align with PCB and connections to denford Orac
    [rpi-gpio-lathe.hal]
2022-09-08 Test using not function to invert limit switches
    [rpi-gpio-lathe.hal]
2022-09-08 Use same pin for both x and z limits
    [rpi-gpio-lathe.hal]
2022-09-08 Use separate limit switches for each axis
    [rpi-gpio-lathe.hal]
2022-09-08 Correct z limit switch debound connection
    [rpi-gpio-lathe.hal]
2022-09-08 Invert the axis enable signals
    [rpi-gpio-lathe.hal]
2022-09-08 Add spindle feedback control and spindle-at-speed settings
    [rpi-gpio-lathe.hal]
2022-09-08 Add spindle-at-speed feedback
    [rpi-gpio-lathe.hal]
2022-09-08 Add UI spindle at speed LED in UI
    [rpi-gpio-lathe-postui.hal]
2022-09-08 Attach spindle speed to detected spindle speed instead of commanded speed
2022-09-08 Use spindle velocity
    [rpi-gpio-lathe-postui.hal]
2022-09-08 Turn RPS to RPM
    [rpi-gpio-lathe-postui.hal]
2022-09-08 Load scale and lowpass for UI calculations
    [rpi-gpio-lathe.hal]
2022-09-08 Add absolute function to threads
    [rpi-gpio-lathe.hal]
2022-09-08 Add functions to threads
    [rpi-gpio-lathe.hal]
2022-09-09 Update EMC VERSION number for the ini file to shut linuxcnc quiet
    [rpi-gpio-lathe.ini]
2022-09-09 Update for acceleration and speed of stepper drivers
    [rpi-gpio-lathe.hal, rpi-gpio-lathe.ini]
2022-09-09 Add a couple more useful manuals
2022-09-09 Update accel settings for axes and traj section
    [rpi-gpio-lathe.ini]
2022-09-13 Update the spindle speed section to simplify the display
    [rpi-gpio-lathe-postui.hal, rpi-gpio-lathe.hal]
2022-09-14 Calculate scale for both stepper motor axis
    [rpi-gpio-lathe.ini]
2022-09-14 Include gmnoccapy macros for lathe wizards
    [rpi-gpio-lathe.ini]
2022-09-14 Start addition of gmoccapy user interface
    [rpi-gpio-lathe-gmoccapy.ini]
2022-09-14 Add missing HALUI in case that fixes the issue
    [rpi-gpio-lathe-gmoccapy.ini]
2022-09-14 Update to get new subcroutine path in
    [rpi-gpio-lathe-gmoccapy.ini]
2022-09-14 Return normal ini file to axis
    [rpi-gpio-lathe.ini]
2022-09-15 Attach spindle feedback to UI components of gmoccapy
    [rpi-gpio-lathe-postui-gmoccapy.hal]
2022-09-15 Update Axis acceleration and velocities
    [rpi-gpio-lathe-gmoccapy.ini]
2022-09-15 Update acceleration curves a bit more
    [rpi-gpio-lathe-gmoccapy.ini]
2022-09-15 Update some spindle and general lathe settings
    [rpi-gpio-lathe-gmoccapy.ini, rpi-gpio-lathe.hal]
2022-09-15 Update the spindle scale preferences
2022-09-15 Add PID control to spindle
    [rpi-gpio-lathe.hal]
2022-09-15 Fix some issues with PID. Partial Fixes
    [rpi-gpio-lathe.hal]
2022-09-15 Update PID section for spindle
    [rpi-gpio-lathe.hal]
2022-09-15 Only use scale.0.out once
    [rpi-gpio-lathe.hal]
2022-09-15 Add P gain
    [rpi-gpio-lathe.hal]
2022-09-15 Update PID to passthrough velocity
    [rpi-gpio-lathe.hal]
2022-09-15 PID FF0 correction
    [rpi-gpio-lathe.hal]
2022-09-15 Add openloop ini file also
    [rpi-gpio-lathe-gmoccapy-openloop.ini]
2022-09-15 Make the ini openloop file use the openloop hal
    [rpi-gpio-lathe-gmoccapy-openloop.ini]
2022-09-15 Fix issue with HAL file
    [rpi-gpio-lathe-gmoccapy-openloop.ini]
2022-09-26 Rename spindle net
    [rpi-gpio-lathe.hal]
2022-09-26 Add openloop configuration for the spindle
    [rpi-gpio-lathe-openloop.hal]
2022-09-26 Add sum2 function to the servo thread
    [rpi-gpio-lathe.hal]
2022-09-26 Add sum2 0 function to servo thread
    [rpi-gpio-lathe.hal]
2022-09-26 First working PID closed loop spindle control
    [rpi-gpio-lathe.hal]
2022-09-27 PID control of spindle fix
    [rpi-gpio-lathe.hal]
2022-09-27 Improve readability of openloop hal
    [rpi-gpio-lathe-openloop.hal]
2022-09-27 Update lathe config for near signal UI
    [rpi-gpio-lathe.hal]
2022-09-27 Add RPM based signals to near for spindle speed
    [rpi-gpio-lathe.hal]
2022-10-12 Adjust the output gain of the 0-10V outputs
    [controller.kicad_sch, pwmfilter.kicad_sch]
2022-10-12 Add spindle enable signal to IO
    [rpi-gpio-lathe.hal]
2022-10-12 Adjust comments in main gmoccapy ini file
    [rpi-gpio-lathe-gmoccapy.ini]
2026-02-26 Update to linuxcnc 2.9.8 (#1)
    * Add new VFD manuals
    * Add relay boad datasheet
    * Align with previous configuration
    * Update to latest LatheMacros
    * Update readme and remove old content
    * Update general UI preferences
    * Add a closed-loop spindle control version HAL
    * Correct scaling for new VFD and motor in open loop
    [lathe_macros.ini, rpi-gpio-lathe-axis-openloop.ini, rpi-gpio-lathe-closedloop.hal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]
